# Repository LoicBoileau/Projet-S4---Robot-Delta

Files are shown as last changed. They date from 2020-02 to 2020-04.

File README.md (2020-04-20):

# Projet-S4---Robot-Delta
Projet de session hiver 2020 Équipe 1 Université de Sherbrooke - Robot Delta

## Licence MIT
Puisque notre projet est en open source, nous avons opté pour une licence MIT, car c'est une licence très permissive et très simple. Elle permet à tous les utilisateurs d'utiliser notre projet à leur guise, c'est-à-dire le modifier, le distribuer, l'utiliser à des fins commerciales ainsi que l'utiliser en privé. Toutefois, nous n'avons pas de garantie sur ce qui arrive avec ceux qui utilisent notre projet et ils ne peuvent pas nous poursuivre si jamais ils se blessent ou autre.

Pour une description complète de la License, voir le fichier License.

## Partie mécanique
Pour voir la liste des matériaux, les étapes d'assemblage du robot ainsi qu'une description des fichiers et des pièces, allez voir dans le fichier Robot_Delta_CAD.

## Partie vision
Pour voir le code de la vision, allez voir dans le fichier vision.

## Mathématiques du modèle
Une simulation physique a été conçue pour décrire la cinématique directe et inverse du robot.
-Disponible [ici](https://github.com/LoicBoileau/Projet-S4---Robot-Delta/tree/master/Simulations%20Physiques).

## Programmer les moteurs
Pour programmer les moteurs Dynamixel, il faut aller consulter le fichier "README" dans le répertoire "Controle_moteurs" 

## Requis pour l'Interface graphique
### Composantes
  - RaspberryPi avec python 3.4 installé (ou une version moins récente)
  - Python 3.4 32 bits installé sur un ordinateur pour programmer sur un ordinateur 
  - Librairies PySide et PySerial installées dans python 3.4 ou dans un environnement virtuel
  - IDE de programmation pour python (i.e. Visual Studio ou Visual Studio Code)
  
### Fonctionnement
L'interface graphique est codée en python et se compile à l'aide du fichier principal (GUI.py) et le fichier de widgets (mainwindow34.py et mainwindow34.ui
Le fichier mainwindow34.py est composé à partir du .ui qui lui se modifie à l'aide du designer.exe de QT. Donc pour modifier le fichier mainwindow34.py, 
il est nécessaire de suivre les instructions suivantes.

### Main pour Interface graphique
GUI.py est le main pour l'interface graphique et dépend du fichier de setup du UI appelé Mainwindow34.py

### Designer .UI
Pour accéder au designer de .ui de Qt, accéder au virtualEnvironnement ou le dossier contenant les librairies de python 3.4.
Dans le fichier, aller ensuite dans "Lib", "site-packages", "PySide"  et trouver le .exe appelé "designer.exe".

### Convertir .ui à .py 
Il est nécessaire de convertir le .ui à .py. Pour ce faire, aller dans le menu de VS "outils" ou "tools", ensuite aller dans "ligne de commande", 
"invite de commande développeur" et entrer les deux commandes suivantes :
* cd Controls
* pyside-uic Mainwindow.ui -o Mainwindow34.py

### Création de l'environnement virtuel à programmer
Pour programmer le UI, il faut un environnement virtuel qui contient les librairies utilisées. (PySide et PySerial)
Pour que les librairies soient disponibles, il est nécessaire de télécharger python3.4 32bits. Ensuite, soit par Visual Studio 
ou par l'invite de commande, installer les librairies.

### Installation des paquets sur le Raspberry Pi
* Installer l'image qui se trouve au lien suivant: https://github.com/UdeS-GRO/pi-gen et installer les paquets mentionnés dans le dossier stage5;
* Ensuite il faut installer python3.4 avec la commande: sudo apt-get install python3.4;
* Installer pip avec la commande: sudo apt-get install python3-pip;
* Installer PySide avec la commande: sudo apt-get install python3-pyside;
* Installer PySerial avec la commande: python3 -m pip install pyserial.

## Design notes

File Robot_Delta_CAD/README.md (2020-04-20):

# ReadMe pour les CAD du robot Delta.
## Descriptions des pièces de l'assemblage
* La plateforme supérieure sert à supporter l'ensemble du robot. 

* Les équerres permettent de soutenir les moteurs à la plateforme.

* Les moteurs utilisés sont les Dynamixel XL-430. 

* Le biceps est le premier bras (supérieur, celui qui est le plus court).

* L'avant-bras est le second bras (inférieur, celui qui est plus long) qui est d'une longueur de 25 cm.

* Les « *turnbuckles* » sont utilisés pour accorder plus de liberté au mouvement de rotation des biceps avec les avant-bras ainsi qu'aux avant-bras avec l'effecteur. Ils sont achetés tels quels au lien suivant: https://traxxas.com/products/parts/3745.

* Le « Fixateur_Bicep_Turnbuckle » sert à empêcher que le « *turnbuckle* » supérieur, celui attaché au biceps, puisse se déplacer horizontalement ou tourner. 

* Les gaines thermorétrécissables sont chauffées à l'aide d'un pistolet thermique « *Heat Gun* ». Son but est d'empêcher le mouvement vertical des avant-bras. 

* L'attache_Turnbuckle_Effecteur sert à relier le « *turnbuckle* » inférieur à l'effecteur.

* L'effecteur est la pince elle-même. 

* Le dossier « Piece_Electroaimant » contient toutes les pièces pour l'assemblage de l'électroaimant à l'effecteur. 

* Dechet_Poubelle et Dechet_Recyclage sont des déchets de différentes couleurs avec un aimant permettant au robot de les prendre avec l'électroaimant et de les trier dans les bacs correspondants. 

* Bac_Poubelle et Bac_Recyclage sont deux bacs permettant aux déchets d'être triés.

* Aluminium_Extrusion est la pièce qui a été utilisée pour faire l'assemblage de la base du robot. 

* Planche_De_Travail est la planche d'opération du robot, c'est-à-dire où les bacs ainsi que les déchets sont situés.

## Description des assemblages
* L'assemblage du robot est contenu dans le fichier « Assemblage_Robot_Delta ».

* L'assemblage pour l'environnement de travail du robot est dans le fichier « Assemblage_Robot_Delta_Avec_Base ».

## Méthodes de confection des pièces
* Toutes les pièces en bois sont découpées à l'aide d'une découpeuse laser. 

* Les autres pièces sont imprimées à l'aide d'une imprimante 3D.

## Étapes d'assemblage
1. Assembler la base du robot à l'aide des extrudés d'aluminium.

2. Ensuite, assembler les équerres à la plaque supérieure à l'aide de 2 vis M4 à tête cylindrique à six pans creux avec des écrous par équerre. Refaire cette opération trois fois.

3. Par la suite, assembler les moteurs aux équerres à l'aide de quatre vis M2 à tête cylindrique bombée à empreinte cruciforme et de rondelles « washer » par équerre. Refaire cette opération trois fois.

4. Assembler les biceps aux moteurs à l'aide de quatre vis M2 à tête cylindrique bombée à six pans creux, par moteur, qui filtre le bois du biceps lorsque la vis entre et qui se rend aux coupleurs du moteur. Refaire cette opération trois fois.

5. Assembler les « *turnbuckles* » aux biceps en enlevant un des bouts des « *turnbuckles* » pour qu'ils puissent s'insérer dans le trou du biceps. Refaire cette opération trois fois.

6. Remettre le bout enlevé des « *turnbuckles* ». Refaire cette opération trois fois.

7. Insérer le « Fixateur_Bicep_Turnbuckle » de chaque côté du biceps et le serrer à l'aide d'une vis M4 à tête cylindrique à six pans creux et d'un écrou par « Fixateur_Bicep_Turnbuckle », ce qui empêchera que les « *turnbuckles* » puissent se déplacer horizontalement ainsi que les rotations, sauf sur eux-mêmes. Refaire cette opération trois fois. 

8. Insérer « Attache_Turnbuckle_Effecteur » aux « *turnbuckles* » seulement en les poussant. Refaire cette opération trois fois. 

9. Insérer deux vis M4 à tête cylindrique à six pans creux avec des écrous par                       « Attache_Turnbuckle_Effecteur » pour empêcher le mouvement horizontal des « *turnbuckles* » ainsi que les mouvements de rotation, sauf sur eux-mêmes encore une fois. Refaire cette opération trois fois.

10. Insérer les six tiges (avant-bras) dans les trous des « *turnbuckles* ».

11. Découper les gaines thermorétrécissables en longueur de 1 cm 24 fois. (Quatre gaines thermorétrécissables par avant-bras).

12. Pour un avant-bras: chauffer les morceaux de gaines thermorétrécissables pour empêcher que les   « *turnbuckles* » sortent de la tige. Il faut donc chauffer un morceau de gaine thermorétrécissable à chaque bout de la tige et les deux autres morceaux sont espacés par les « *turnbuckles* ». Cela fait en sorte que les « *turnbuckles* » ne peuvent pas se déplacer en translation et qu'ils sont situés aux extrémités des avant-bras. 

13. Prendre l'électroaimant et l'insérer dans son support respectif. Si ce dernier tombe de son support, utiliser des vis M2 à tête cylindrique bombée à six pans creux pour qu'il reste en place.

14. Visser le support de l'électroaimant à l'effecteur à l'aide de quatre vis M4 à tête cylindrique à six pans creux avec des écrous.

15. Visser les « Attache_Turnbuckle_Effecteur » à l'effecteur à l'aide de deux vis M4 à tête cylindrique à six pans creux avec des écrous. Refaire cette opération trois fois. 

16. Attacher la plaque supérieure aux extrudés d'aluminium. 

## Liste des composantes *BOM (Bill Of Materials)*
1. 1 plaque supérieure en bois;
2. 3 équerres en plastique;
3. 3 moteurs dynamixel XL-430;
4. 3 biceps en bois;
5. 6 « Fixateur_Bicep_Turnbuckle » en plastique;
6. 6 « *turnbuckles* »;
7. 6 avant-bras de longueur de 25 cm en métal;
8. 3 « Attache_Turnbuckle_Effecteur » en plastique;
9. 1 électroaimant;
10. 24 morceaux de gaine thermorétrécissable de longueur de 1 cm;
11. 1 support à électroaimant en plastique;
12. 1 effecteur en bois;
13. 28 vis M4 à tête cylindrique à six pans creux avec des écrous respectifs;
14. 12 vis M2 à tête cylindrique bombée à six pans creux avec 12 rondelles respectives;
15. 12 vis M2 à tête cylindrique bombée à empreinte cruciforme.

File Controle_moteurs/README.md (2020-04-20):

### Programmer les moteurs
Pour programmer les moteurs Dynamixel, il faut le IDE d'Arduino avec la librairie de OpenCR.
Il faut également que les moteurs soient alimentés par une source d'alimentation externe, car l'alimentation fournie par le port USB de
l'ordinateur n'est pas suffisante au fonctionnement des moteurs.
La programmation n'est pas très complexe, puisque la librairie contient des exemples de codes qui 
permettent de facilement intégrer la fonctionnalité désirée. Les liens suivants dirigent vers les tutoriels appropriés.
Il est nécessaire de suivre les tutoriels afin d'identifier les moteurs. Afin de spécifier un déplacement des moteurs selon la 
position déterminée, il s'agit de copier dans le IDE d'Arduino le code Controle_Moteur qui permet d'utiliser les 3 moteurs contrairement 
à celui des librairies qui n'en contrôle qu'un seul.

http://emanual.robotis.com/docs/en/parts/controller/opencr10/
http://emanual.robotis.com/docs/en/software/dynamixel/dynamixel_workbench/

Les nombres spécifiés en paramètres dans la fonction "goalPosition" ne doivent pas dépasser 4096, qui est la résolution de chaque moteur.
Si une telle situation survient, il faut téléverser le programme à nouveau, car les moteurs vont tomber en "erreur". Pour un angle de
90 degrés, par exemple, il faut spécifier 1024 et ajuster par la suite, car la position 0 de chaque moteur n'est pas nécessairement la 
même. Il est également nécessaire de spécifier un délai minimal pour s'assurer que les moteurs atteignent leur position avant que le
prochain ne soit appelé.

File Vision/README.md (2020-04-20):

# ReadMe pour la vision.
## Étapes pour faire fonctionner la vision
* Installer pip avec la commande: sudo apt-get install python3-pip (si ce n'est pas fait);
* Installer la librairie OpenCV avec la commande: pip install opencv-python==3.4.1.15;
* Installer la librairie numpy avec la commande: pip install numpy;
* Installer la librairie csv avec la commande: pip install csv; 
* Se connecter au Raspberry Pi avec un écran et un clavier;
* Brancher la Webcam au RaspberryPi via la prise USB;
* Exécuter le code dans Python IDLE ou autre et prendre la planche de travail en photo lorsque souhaité;
* Pour la documentation du code allez voir les commentaires dans ce dernier.

## Informations utiles
* À cause de la distanciation sociale, il a été impossible d'intégrer la vision au robot c'est pourquoi la touche espace est présente pour prendre les photos. 

* Pour les tests, l'IDE PyCharm sur un ordinateur personnel a été utilisé, dans le but d'avoir plus de rapidité de traitement d'image ainsi qu'une meilleure qualité de caméra. Cependant, le code fonctionne très bien sur le Raspberry Pi. Il suffit d'utiliser Python IDLE et d'exécuter le code. 
  
## Sources utilisées
* Pour le calcul du centre de masse: https://www.learnopencv.com/find-center-of-blob-centroid-using-opencv-cpp-python/
* Pour l'algorithme de détection de contours: https://www.youtube.com/watch?v=6AY5p1uC5gM

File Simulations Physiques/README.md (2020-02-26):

# Simulations Physiques

DeltaRobot

## Simulation MotionGenesis

Logiciel de simulation physique, semblable à MatLab, permettant de faire des opérations vectorielles.
>Disponible [ici](http://www.motiongenesis.com/). 

 Est utilisé pour faire la cinématique directe et, éventuellement, la cinématique inverse.

### Cinématique directe
Description statique du robot. 
- Prend en **entrée** les angles &theta;<sub>1</sub>, &theta;<sub>2</sub> et &theta;<sub>3</sub> des moteurs.
- Donne en **sortie** la position P(x,y,z) de la "pince" du robot.

Est décrit par le fichier **MotionGenesis.txt**.

### Cinématique inverse
Description statique du robot. 
- Donne en **sortie** la position P(x,y,z) de la "pince" du robot.
- Prend en **entrée** les angles &theta;<sub>1</sub>, &theta;<sub>2</sub> et &theta;<sub>3</sub> des moteurs.

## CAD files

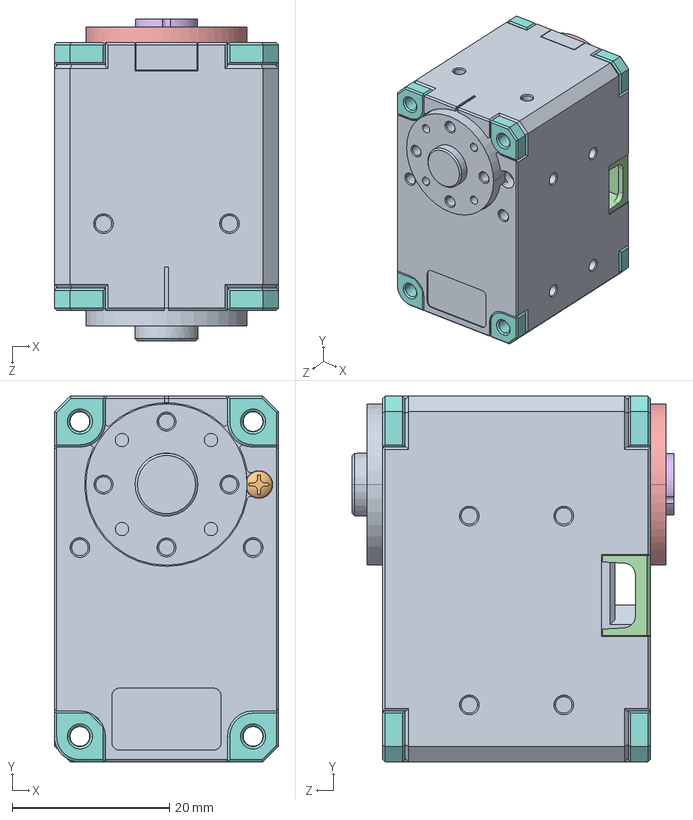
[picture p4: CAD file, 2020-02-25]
Robot_Delta_CAD/XL-430_new.SLDASM
28.5 x 46.5 x 40.9 mm
DC11_A01_DUMMY.stp
DX124_SCREW-COVER.stp
B3B-EH.stp x 2
DC11_A01_CASE_CVR_DUMMY.stp
DC11_A01_IDLER_DUMMY.stp
DC11_A01_IDLER_CAP_DUMMY.stp
DC11_A01_IDLER_SCREW.stp
DC11_A01_SPACER_DUMMY.stp x 8

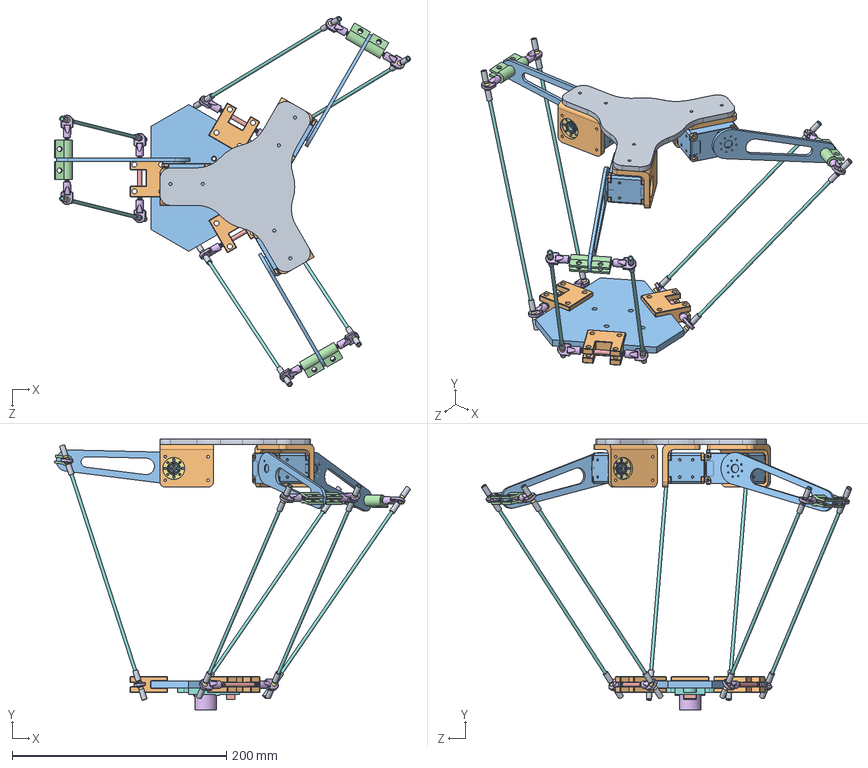
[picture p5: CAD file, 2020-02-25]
Robot_Delta_CAD/Assemblage_Robot_Delta.SLDASM
332.4 x 253.0 x 345.9 mm
Plaque_Support
Equerre_Moteur x 3
DC11_A01_DUMMY.stp x 3
DX124_SCREW-COVER.stp x 3
B3B-EH.stp x 6
DC11_A01_CASE_CVR_DUMMY.stp x 3
DC11_A01_IDLER_DUMMY.stp x 3
DC11_A01_IDLER_CAP_DUMMY.stp x 3
DC11_A01_IDLER_SCREW.stp x 3
DC11_A01_SPACER_DUMMY.stp x 24
Bicep x 3
Fixateur_Bicep_Turnbuckle x 6
Rod_Turnbuckle x 6
Attache_Rod_Boule_Turnbuckle x 12
Boule_Turnbuckle x 12
Avant_bras x 6
Gaine_Thermoretrecissable x 24
Attache_Turnbuckle_Effecteur x 3
Effecteur
PCB_Electroaimant
Connecteur_Electroaimant
Electroaimant
pan cross head screw_as
Support_Electroaimant

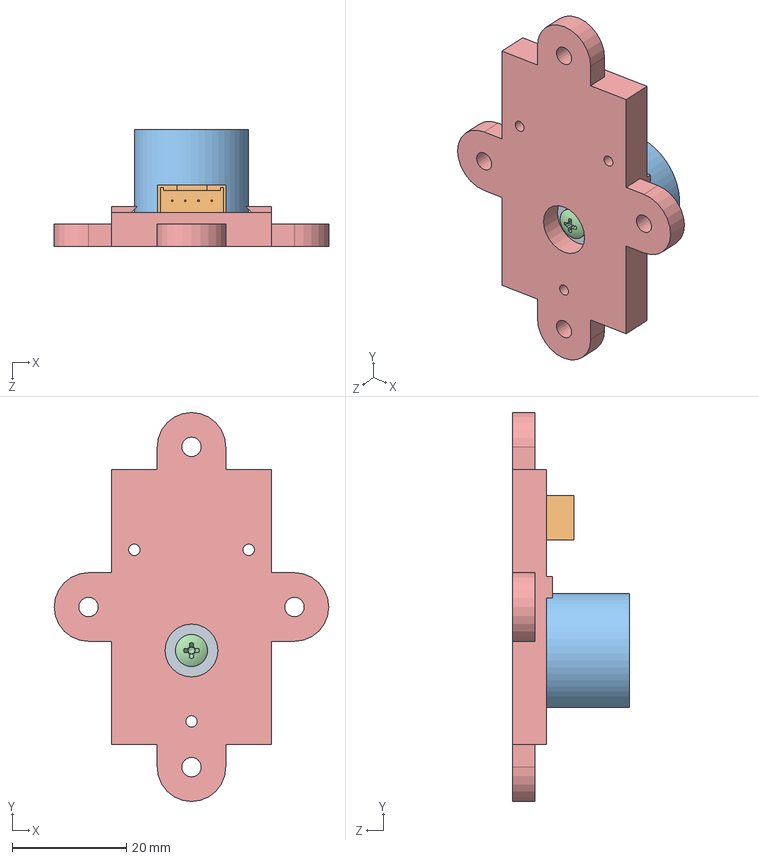
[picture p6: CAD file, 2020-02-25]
Robot_Delta_CAD/Piece_Electroaimant/Assemblage_Electroaimant.SLDASM
48.0 x 68.0 x 20.5 mm
PCB_Electroaimant
Connecteur_Electroaimant
Electroaimant
pan cross head screw_as
Support_Electroaimant

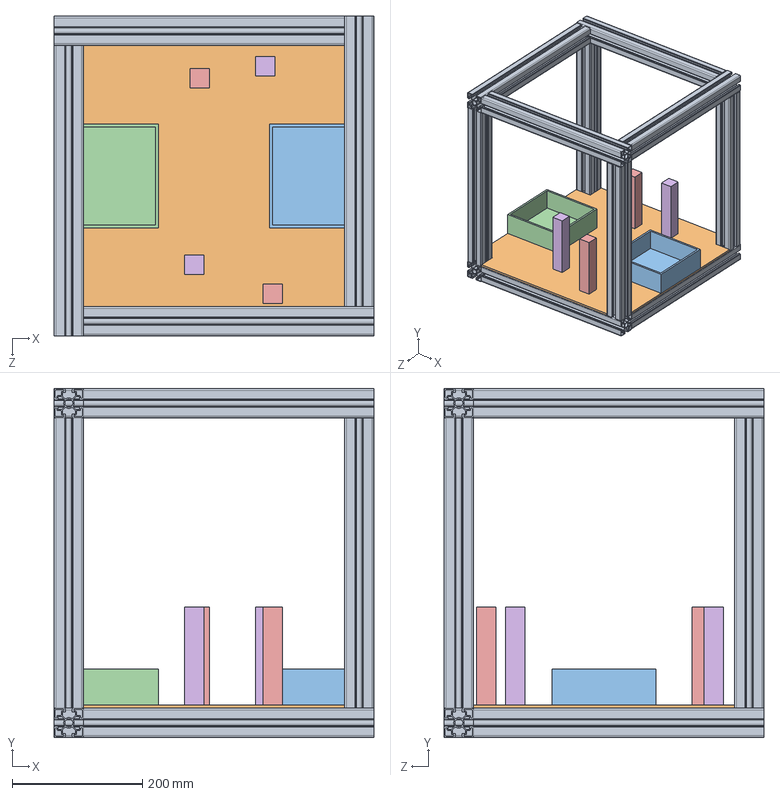
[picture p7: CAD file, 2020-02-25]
Robot_Delta_CAD/Assemblage_Robot_Delta_Avec_Base.SLDASM
490.0 x 535.0 x 490.0 mm
Aluminium_Extrusion x 12
Planche_De_Travail
Bac_Poubelle
Bac_Recyclage
Dechet_Poubelle x 2
Dechet_Recyclage x 2

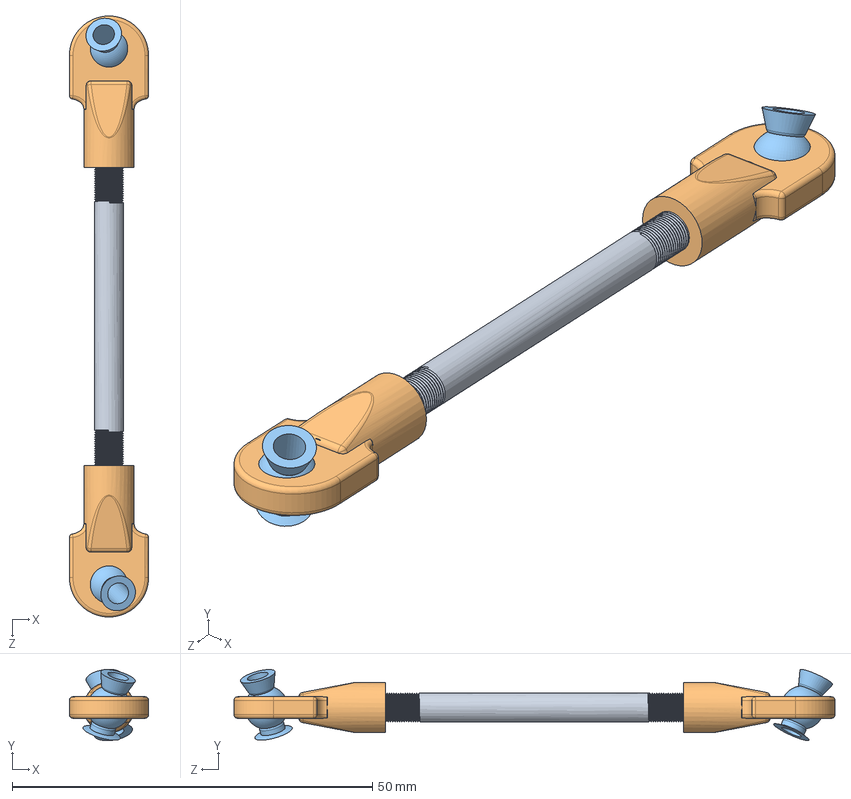
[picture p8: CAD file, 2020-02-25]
Robot_Delta_CAD/Turnbuckle.SLDASM
11.0 x 9.90 x 83.4 mm
Rod_Turnbuckle
Attache_Rod_Boule_Turnbuckle x 2
Boule_Turnbuckle x 2

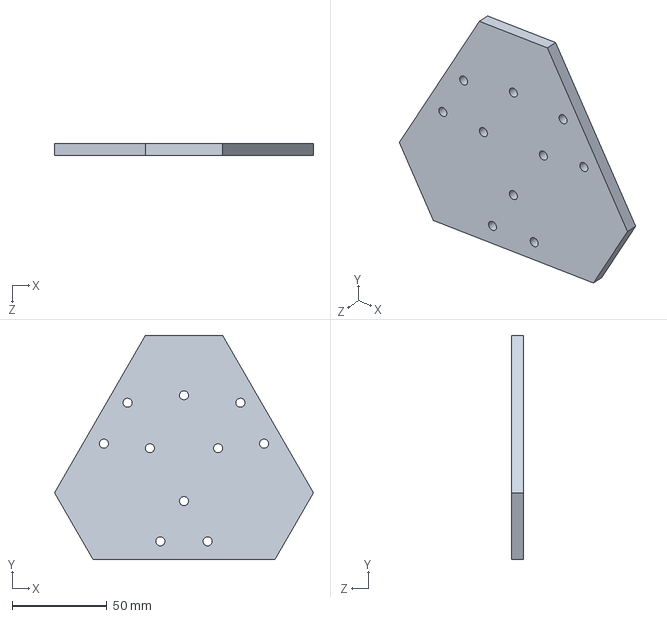
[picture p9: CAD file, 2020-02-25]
Robot_Delta_CAD/Effecteur.SLDPRT
137.0 x 118.6 x 6.35 mm

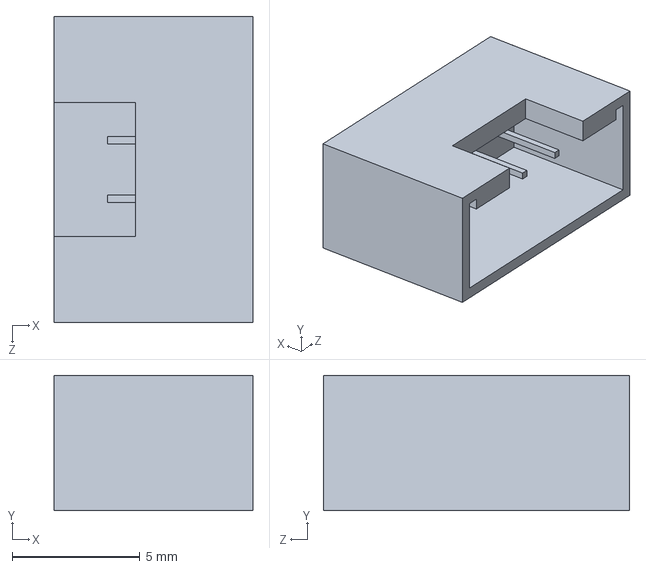
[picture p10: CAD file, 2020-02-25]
Robot_Delta_CAD/Piece_Electroaimant/Connecteur_Electroaimant.SLDPRT
7.80 x 5.30 x 12.0 mm

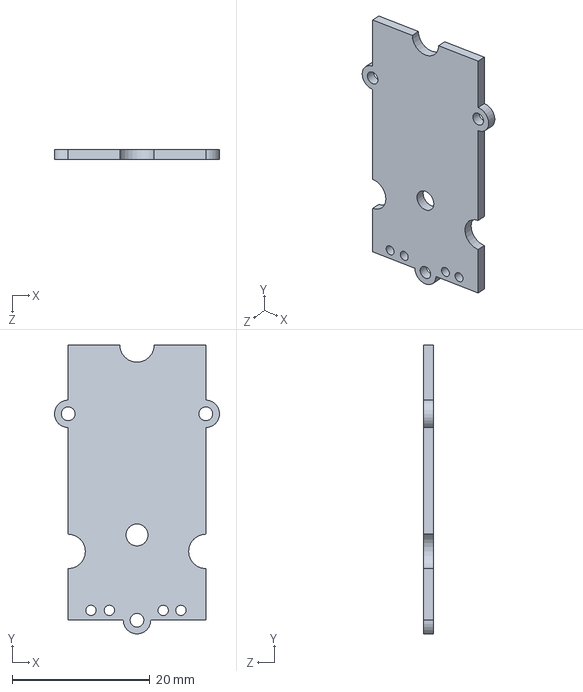
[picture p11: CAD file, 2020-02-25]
Robot_Delta_CAD/Piece_Electroaimant/PCB_Electroaimant.SLDPRT
24.0 x 42.0 x 1.50 mm

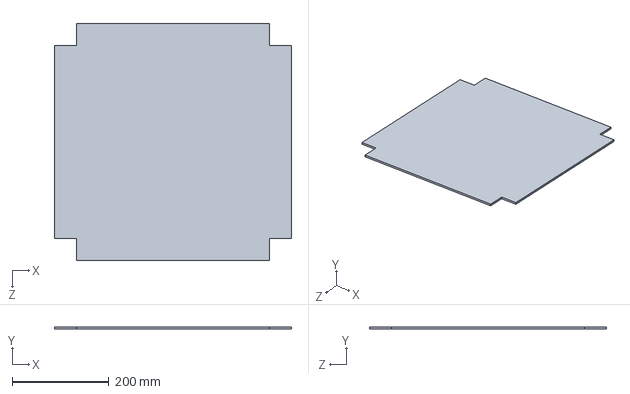
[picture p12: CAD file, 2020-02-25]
Robot_Delta_CAD/Planche_De_Travail.SLDPRT
490.0 x 5.00 x 490.0 mm

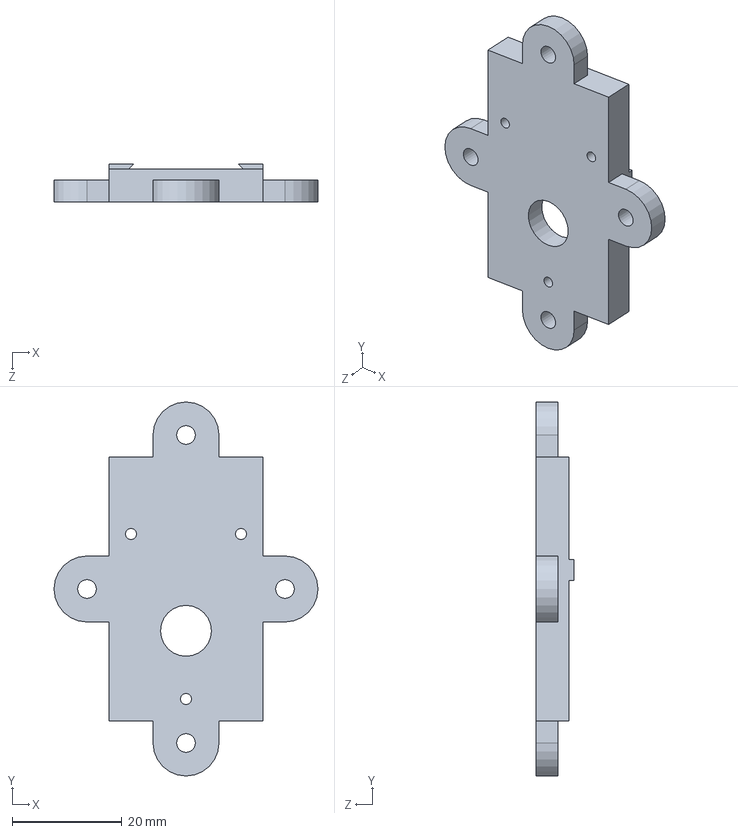
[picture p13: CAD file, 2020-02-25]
Robot_Delta_CAD/Piece_Electroaimant/Support_Electroaimant.sldprt
48.0 x 68.0 x 7.00 mm

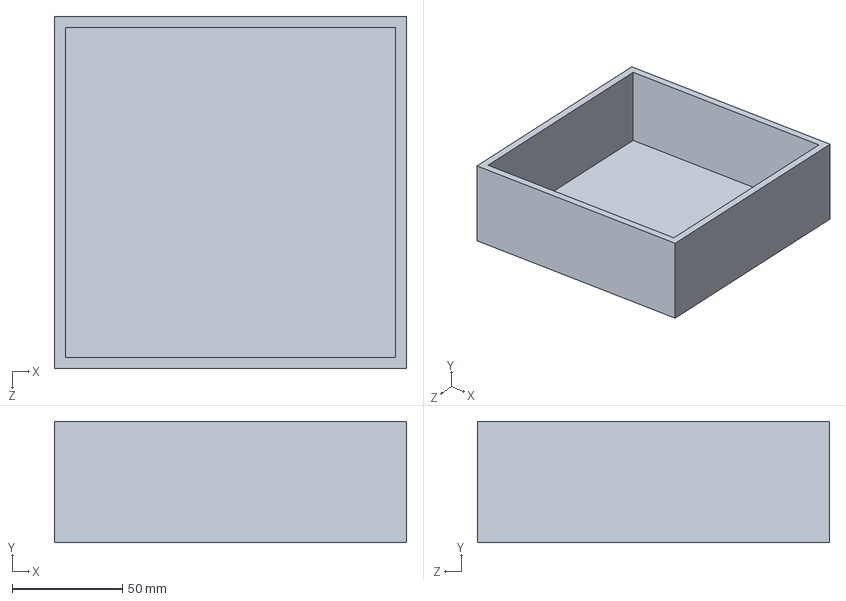
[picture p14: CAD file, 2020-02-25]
Robot_Delta_CAD/Bac_Recyclage.SLDPRT
160.0 x 55.0 x 160.0 mm

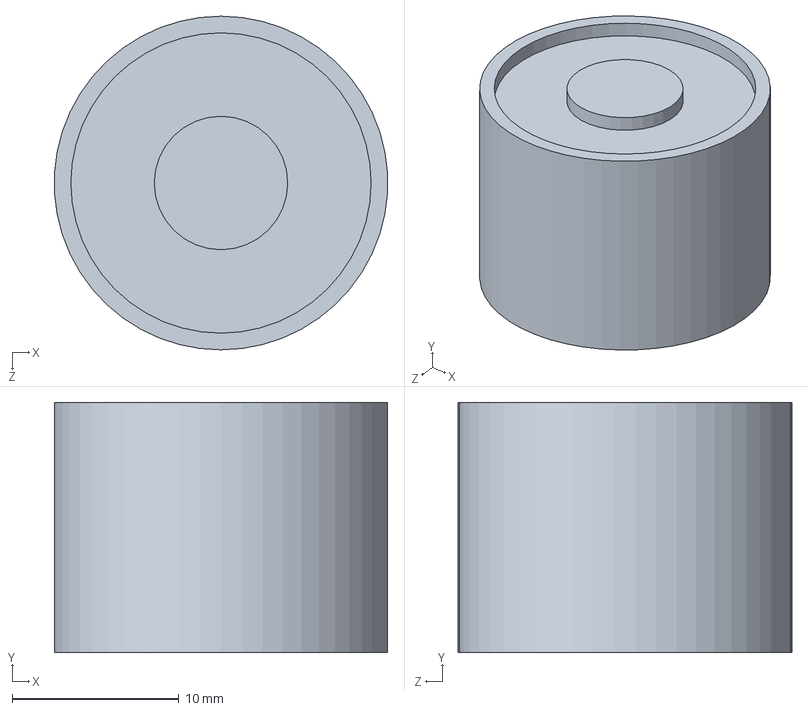
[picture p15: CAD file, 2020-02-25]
Robot_Delta_CAD/Piece_Electroaimant/Electroaimant.SLDPRT
20.0 x 15.0 x 20.0 mm

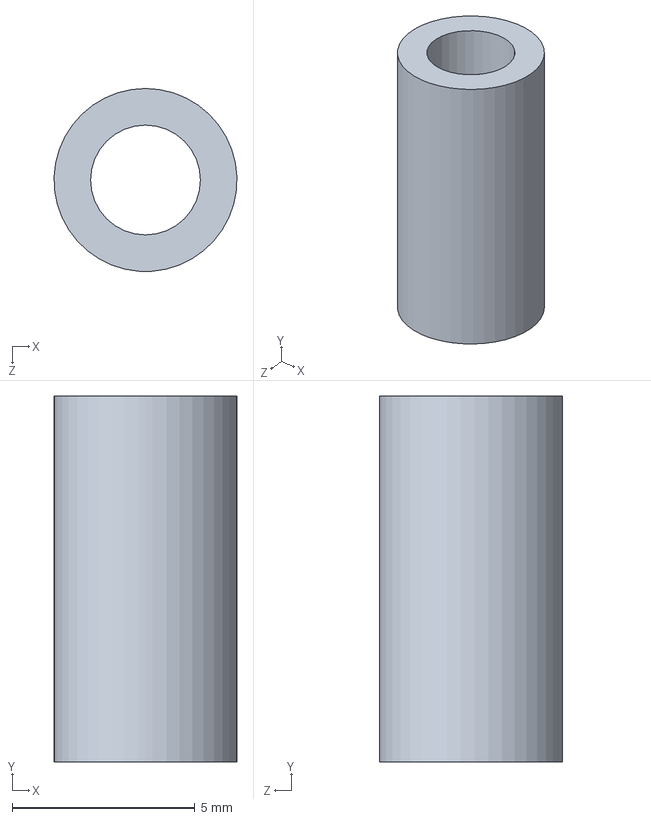
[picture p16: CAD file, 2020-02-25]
Robot_Delta_CAD/Gaine_Thermoretrecissable.SLDPRT
5.00 x 10.0 x 5.00 mm

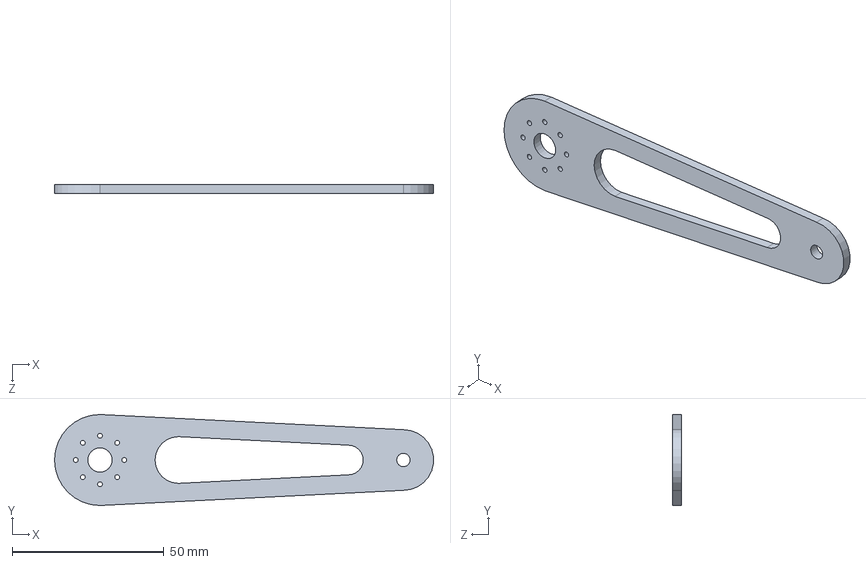
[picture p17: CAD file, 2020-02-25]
Robot_Delta_CAD/Bicep.SLDPRT
124.9 x 30.0 x 3.00 mm

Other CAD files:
Robot_Delta_CAD/Avant_bras.SLDPRT
Robot_Delta_CAD/Dechet_Recyclage.SLDPRT
Robot_Delta_CAD/Plaque_Support.SLDPRT
Robot_Delta_CAD/Bac_Poubelle.SLDPRT
Robot_Delta_CAD/Aluminium_Extrusion.SLDPRT
Robot_Delta_CAD/Attache_Rod_Boule_Turnbuckle.SLDPRT
Robot_Delta_CAD/Attache_Turnbuckle_Effecteur.SLDPRT
Robot_Delta_CAD/Boule_Turnbuckle.SLDPRT
Robot_Delta_CAD/Dechet_Poubelle.SLDPRT
Robot_Delta_CAD/Equerre_Moteur.SLDPRT
Robot_Delta_CAD/Fixateur_Bicep_Turnbuckle.SLDPRT
Robot_Delta_CAD/Rod_Turnbuckle.SLDPRT

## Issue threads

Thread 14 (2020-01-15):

Faire tourner les moteurs

nguwuyen, 2020-01-15:

alexfilion, 2020-02-19:
Trouver sur Visual Studio comment envoyer un certain courant au moteur pour le faire tourner.
Faire des tests pour comprendre son encodeur et pouvoir l'arrêter à la valeur que l'on veut.

Closed 2020-02-21.

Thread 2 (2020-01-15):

En tant qu'utilisateur, je veux que le robot soit supporté à un point fixe

LoicBoileau, 2020-01-15:
- Structure en Aluminium (idée)

nguwuyen, 2020-02-13:
Frame

Closed 2020-04-17.

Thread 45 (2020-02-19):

Cinématique Direct

alexfilion, 2020-02-19:
Faire les mathématiques pour trouver les coordonnées du robot selon des angles que les moteurs ont.
Trouver les équations les reliant.

alexfilion, 2020-02-19:
Faire les mathématiques pour trouver les angles des moteurs si on donne une coordonnée.
Trouver les équations les reliant.

Closed 2020-04-01.

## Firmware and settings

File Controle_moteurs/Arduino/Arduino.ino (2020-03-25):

/* Authors: Loic Boileau */

#include <DynamixelWorkbench.h>

#if defined(__OPENCM904__)
  #define DEVICE_NAME "3" //Dynamixel on Serial3(USART3)  <-OpenCM 485EXP
#elif defined(__OPENCR__)
  #define DEVICE_NAME ""
#endif   

#define BAUDRATE        57600
#define DXL_ID1         2
#define DXL_ID2         3
#define DXL_ID3         1

#define LENGTH_MESSAGE  8
#define DECA_MOT3       200

uint8_t dxl_id1 = DXL_ID1;
uint8_t dxl_id2 = DXL_ID2;
uint8_t dxl_id3 = DXL_ID3;

int32_t theta1 = 0;
int32_t theta2 = 0;
int32_t theta3 = 0;

int32_t msgArg1 = 0;
int32_t msgArg2 = 0;
int32_t msgArg3 = 0;

int cmdNb = 0;

uint32_t maxPosMotor1 = 2500;
uint32_t maxPosMotor2 = 2500;
uint32_t maxPosMotor3 = 2500;

uint32_t minPosMotor1 = 1000;
uint32_t minPosMotor2 = 1000;
uint32_t minPosMotor3 = 800; //valeur des autres moteurs - DECA_MOT3(200)

DynamixelWorkbench dxl_wb;

bool commandReceived = false;

void setup() 
{  
  Serial.begin(57600);
  // while(!Serial); // Wait for Opening Serial Monitor

  Serial.println('Reset of the Open CR');

  const char *log;
  bool result = false;
  
  uint16_t model_number_id1 = 0;
  uint16_t model_number_id2 = 0;
  uint16_t model_number_id3 = 0;

  float decalage_id1 = 0;

  result = dxl_wb.init(DEVICE_NAME, BAUDRATE, &log);
  if (result == false)
  {
    Serial.println(log);
    Serial.println("Failed to init");
  }
  else
  {
    Serial.print("Succeeded to init : ");
    Serial.println(BAUDRATE);  
  }

  result = dxl_wb.ping(dxl_id1, &model_number_id1, &log)&& dxl_wb.ping(dxl_id2, &model_number_id2, &log) && dxl_wb.ping(dxl_id3, &model_number_id3, &log) ;
  if (result == false)
  {
    Serial.println(log);
    Serial.println("Failed to ping");
  }
  else
  {
    Serial.println("Succeeded to ping");
    Serial.print("id motor1 : ");
    Serial.print(dxl_id1);
    Serial.print(" model_number : ");
    Serial.println(model_number_id1);
    Serial.print("id motor2 : ");
    Serial.print(dxl_id2);
    Serial.print(" model_number : ");
    Serial.println(model_number_id2);
    Serial.print("id motor3 : ");
    Serial.print(dxl_id3);
    Serial.print(" model_number : ");
    Serial.println(model_number_id3);
  }

  result = dxl_wb.jointMode(dxl_id1, 0, 0, &log) && dxl_wb.jointMode(dxl_id2, 0, 0, &log) && dxl_wb.jointMode(dxl_id3, 0, 0, &log);
  if (result == false)
  {
    Serial.println(log);
    Serial.println("Failed to change joint mode");
  }
  else
  {
    Serial.println("Succeed to change joint mode");
    Serial.println("Dynamixel is moving...");

    for (int count = 0; count < 1; count++)
    {
      dxl_wb.goalPosition(dxl_id1, (int32_t)1000);
      dxl_wb.goalPosition(dxl_id2, (int32_t)1000);
      dxl_wb.goalPosition(dxl_id3, (int32_t)800);
      delay(3000);

      dxl_wb.goalPosition(dxl_id1, (int32_t)2000);
      dxl_wb.goalPosition(dxl_id2, (int32_t)2000);
      dxl_wb.goalPosition(dxl_id3, (int32_t)1800);
      delay(3000);
    }
  }
  
}

void loop() 
{

  if (Serial.available() > 0){
    cmdNb = readData(); //read the available data and return the first short received as the command number

    if ( cmdNb >= 1 ) //make sure the angle received are in a good range and command is for moving motors
      Serial.write((byte)cmdNb);  //write the command Number to confirmed you have received it
      theta1 = msgArg1;
      theta2 = msgArg2;
      theta3 = msgArg3;
      commandReceived = true;
      delay(10);
    }
    else if( cmdNb == 1 ){ //if the command is for something else then dont activate the motors
      Serial.write((byte)cmdNb);
      delay(10);
    }
  
  if (commandReceived){
    checkMaxPosMotors();
        
    dxl_wb.goalPosition(dxl_id1, (int32_t)theta1);
    dxl_wb.goalPosition(dxl_id2, (int32_t)theta2);
    dxl_wb.goalPosition(dxl_id3, (int32_t)theta3-DECA_MOT3);
    
    commandReceived = false;
  }
}

int readData()
{
  byte bytesBuffer[LENGTH_MESSAGE];
  int i = 0;
  while (Serial.available()) {
    delay(10);  
    if (Serial.available() >0) {
      byte Byte = Serial.read();  //gets one byte from serial buffer
      bytesBuffer[i++] = Byte; //makes the string readString
      //Serial.println(bytesBuffer[i]);
    }  
  }
  //Prendre le premier octet et le décaller de 8 bits.
  int commandNb = int((unsigned char)(bytesBuffer[1]) << 8 | (unsigned char)(bytesBuffer[0]));
  
  msgArg1 = int((unsigned char)(bytesBuffer[3]) << 8 | (unsigned char)(bytesBuffer[2])); 
  msgArg2 = int((unsigned char)(bytesBuffer[5]) << 8 | (unsigned char)(bytesBuffer[4]));
  msgArg3 = int((unsigned char)(bytesBuffer[7]) << 8 | (unsigned char)(bytesBuffer[6]));

  return (commandNb);
}

bool checkMaxPosMotors()
{
  bool motorCommandInRange = true;
  if (theta1 > maxPosMotor1){
    theta1 = maxPosMotor1;
    motorCommandInRange = false;
  }
  else if (theta1 < minPosMotor1){
    theta1 = minPosMotor1;
    motorCommandInRange = false;
  }
  if (theta2 > maxPosMotor2){
    theta2 = maxPosMotor2;
    motorCommandInRange = false;
  }
  else if (theta2 < minPosMotor2){
    theta2 = minPosMotor2;
    motorCommandInRange = false;
  }
  if (theta3 > maxPosMotor3){
    theta3 = maxPosMotor3;
    motorCommandInRange = false;
  }
  else if (theta3 < minPosMotor3){
    theta3 = minPosMotor3;
    motorCommandInRange = false;
  }
  return (motorCommandInRange);
}

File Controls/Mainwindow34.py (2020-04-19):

# -*- coding: utf-8 -*-

# Form implementation generated from reading ui file 'Mainwindow.ui'
#
# Created: Sat Apr 18 12:41:44 2020
#      by: pyside-uic 0.2.15 running on PySide 1.2.4
#
# WARNING! All changes made in this file will be lost!

from PySide import QtCore, QtGui

class Ui_MainWindow(object):
    def setupUi(self, MainWindow):
        MainWindow.setObjectName("MainWindow")
        MainWindow.setEnabled(True)
        MainWindow.resize(849, 724)
        self.centralwidget = QtGui.QWidget(MainWindow)
        self.centralwidget.setObjectName("centralwidget")
        self.line = QtGui.QFrame(self.centralwidget)
        self.line.setGeometry(QtCore.QRect(341, 201, 0, 0))
        self.line.setFrameShape(QtGui.QFrame.HLine)
        self.line.setFrameShadow(QtGui.QFrame.Sunken)
        self.line.setObjectName("line")
        self.label_5 = QtGui.QLabel(self.centralwidget)
        self.label_5.setGeometry(QtCore.QRect(40, 14, 80, 20))
        self.label_5.setObjectName("label_5")
        self.comboBoxPort = QtGui.QComboBox(self.centralwidget)
        self.comboBoxPort.setGeometry(QtCore.QRect(90, 15, 221, 20))
        self.comboBoxPort.setObjectName("comboBoxPort")
        self.frame_command1 = QtGui.QFrame(self.centralwidget)
        self.frame_command1.setGeometry(QtCore.QRect(30, 40, 431, 581))
        self.frame_command1.setStyleSheet("")
        self.frame_command1.setFrameShape(QtGui.QFrame.StyledPanel)
        self.frame_command1.setFrameShadow(QtGui.QFrame.Raised)
        self.frame_command1.setObjectName("frame_command1")
        self.label_theta1 = QtGui.QLabel(self.frame_command1)
        self.label_theta1.setGeometry(QtCore.QRect(190, 164, 56, 20))
        self.label_theta1.setAlignment(QtCore.Qt.AlignCenter)
        self.label_theta1.setObjectName("label_theta1")
        self.lineEdit_x = QtGui.QLineEdit(self.frame_command1)
        self.lineEdit_x.setGeometry(QtCore.QRect(45, 54, 130, 20))
        self.lineEdit_x.setStyleSheet("background-color: rgb(255, 255, 255);")
        self.lineEdit_x.setObjectName("lineEdit_x")
        self.button_command = QtGui.QPushButton(self.frame_command1)
        self.button_command.setGeometry(QtCore.QRect(12, 510, 235, 61))
        font = QtGui.QFont()
        font.setPointSize(11)
        self.button_command.setFont(font)
        self.button_command.setStyleSheet("#button_command{\n"
"border: 2px solid;\n"
"background-color: white;\n"
"    border-top-color: rgb(85, 255, 0);\n"
"    border-left-color: rgb(85, 255, 0);\n"
"    border-right-color: rgb(67, 203, 0);\n"
"    border-bottom-color: rgb(67, 203, 0);\n"
"}\n"
"#button_command:pressed{\n"
"    background-color: rgb(85, 255, 0);\n"
"}")
        self.button_command.setObjectName("button_command")
        self.lineEdit_ChangeCommand = QtGui.QLineEdit(self.frame_command1)
        self.lineEdit_ChangeCommand.setGeometry(QtCore.QRect(310, 370, 51, 41))
        font = QtGui.QFont()
        font.setPointSize(11)
        self.lineEdit_ChangeCommand.setFont(font)
        self.lineEdit_ChangeCommand.setStyleSheet("background-color: rgb(255, 255, 255);")
        self.lineEdit_ChangeCommand.setAlignment(QtCore.Qt.AlignCenter)
        self.lineEdit_ChangeCommand.setObjectName("lineEdit_ChangeCommand")
        self.checkBox_cinDir = QtGui.QCheckBox(self.frame_command1)
        self.checkBox_cinDir.setGeometry(QtCore.QRect(12, 26, 411, 20))
        font = QtGui.QFont()
        font.setPointSize(9)
        self.checkBox_cinDir.setFont(font)
        self.checkBox_cinDir.setObjectName("checkBox_cinDir")
        self.lineEdit_y = QtGui.QLineEdit(self.frame_command1)
        self.lineEdit_y.setGeometry(QtCore.QRect(45, 80, 130, 20))
        self.lineEdit_y.setStyleSheet("background-color: rgb(255, 255, 255);")
        self.lineEdit_y.setObjectName("lineEdit_y")
        self.label_z = QtGui.QLabel(self.frame_command1)
        self.label_z.setGeometry(QtCore.QRect(190, 106, 56, 20))
        self.label_z.setAlignment(QtCore.Qt.AlignCenter)
        self.label_z.setObjectName("label_z")
        self.label_6 = QtGui.QLabel(self.frame_command1)
        self.label_6.setGeometry(QtCore.QRect(10, 5, 411, 20))
        font = QtGui.QFont()
        font.setPointSize(9)
        self.label_6.setFont(font)
        self.label_6.setAlignment(QtCore.Qt.AlignCenter)
        self.label_6.setObjectName("label_6")
        self.label_x = QtGui.QLabel(self.frame_command1)
        self.label_x.setGeometry(QtCore.QRect(190, 54, 56, 20))
        self.label_x.setAlignment(QtCore.Qt.AlignCenter)
        self.label_x.setObjectName("label_x")
        self.checkBox_cinInv = QtGui.QCheckBox(self.frame_command1)
        self.checkBox_cinInv.setGeometry(QtCore.QRect(12, 136, 411, 20))
        font = QtGui.QFont()
        font.setPointSize(9)
        self.checkBox_cinInv.setFont(font)
        self.checkBox_cinInv.setObjectName("checkBox_cinInv")
        self.EStop = QtGui.QPushButton(self.frame_command1)
        self.EStop.setGeometry(QtCore.QRect(12, 296, 411, 60))
        font = QtGui.QFont()
        font.setPointSize(22)
        self.EStop.setFont(font)
        self.EStop.setStyleSheet("#EStop {\n"
"border: 2px solid;\n"
"border-radius: 6px;\n"
"\n"
"color: red;\n"
"    border-top-color: rgb(255, 0, 0);\n"
"    border-right-color: rgb(202, 0, 0);\n"
"    border-bottom-color: rgb(202, 0, 0);\n"
"    border-left-color: rgb(255, 0, 0);\n"
"background-color: pink;\n"
"}\n"
"#EStop:pressed \n"
"{ \n"
"background-color: white;\n"
"}")
        self.EStop.setObjectName("EStop")
        self.label_theta3 = QtGui.QLabel(self.frame_command1)
        self.label_theta3.setGeometry(QtCore.QRect(190, 216, 56, 20))
        self.label_theta3.setAlignment(QtCore.Qt.AlignCenter)
        self.label_theta3.setObjectName("label_theta3")
        self.lineEdit_z = QtGui.QLineEdit(self.frame_command1)
        self.lineEdit_z.setGeometry(QtCore.QRect(45, 106, 130, 20))
        self.lineEdit_z.setStyleSheet("background-color: rgb(255, 255, 255);")
        self.lineEdit_z.setObjectName("lineEdit_z")
        self.label_y = QtGui.QLabel(self.frame_command1)
        self.label_y.setGeometry(QtCore.QRect(190, 80, 56, 20))
        self.label_y.setAlignment(QtCore.Qt.AlignCenter)
        self.label_y.setObjectName("label_y")
        self.pushButton_Params = QtGui.QPushButton(self.frame_command1)
        self.pushButton_Params.setGeometry(QtCore.QRect(12, 256, 411, 26))
        self.pushButton_Params.setObjectName("pushButton_Params")
        self.label_theta2 = QtGui.QLabel(self.frame_command1)
        self.label_theta2.setGeometry(QtCore.QRect(190, 190, 56, 20))
        self.label_theta2.setAlignment(QtCore.Qt.AlignCenter)
        self.label_theta2.setObjectName("label_theta2")
        self.button_command_Stop = QtGui.QPushButton(self.frame_command1)
        self.button_command_Stop.setGeometry(QtCore.QRect(323, 510, 100, 61))
        font = QtGui.QFont()
        font.setPointSize(14)
        self.button_command_Stop.setFont(font)
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

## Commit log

2020-01-15 Ajout d'un dossier CAD
2020-01-15 Ajouter fichier texte dans CAD
2020-01-15 Clarifier dossier CAD
2020-02-05 Ajout d'un nouveau fichier python pour le GUI de Qt
2020-02-05 Ajout du fichier GUI.UI dans la solution
2020-02-11 Ajout d'un environnement virtuel en python 3 au cas ou. Ajout du logiciel UI designer de Qt, voir readMe pour trouver la location du fichier.
    [pyvenv.cfg]
2020-02-13 Modification du UI avec Phil, ajout arrêt d'urgence et boutton de commande
2020-02-15 Modification de la location du fichier designer.exe et ajout d'un code pour executer l'interface graphique
2020-02-15 Ajout du fichier .exe pour convertir les fichir .ui en .py. Il suffit simplement d'utiliser la commande dans le fichier readMe
2020-02-16 Ajout d'un main pour l'interface graphiqe. Ajout de la commande pour convertir .ui à .py dans le readMe.
2020-02-16 Régler issue #26 faire clignoter le EStop
    [GUI.py]
2020-02-17 Ajout d'un boutton pour confirmer les coordonnées cartésiennes
2020-02-18 Ajout d'un gestionnaire de thread et d'une loop de temps qui vérifiera à chaque 0.1 s si l'interface graphique c'est fait updater. Modification du fichier requirement.txt
2020-02-18 ajout de checkbox exclusive pour cinematique directe et inverse
2020-02-18 Ajout d'une option de synchronisation pour les ports
2020-02-19 Retirer environnement virtuel RaspberryPi
    [pyvenv.cfg]
2020-02-21 Ajout de fonctionnalitées pour le UI dont le boutton pour envoyer une commande
2020-02-23 Create README.txt pour les CAD du robot
2020-02-23 Ajout de tous les CAD du robot
    [Aluminium_Extrusion.SLDPRT, Assemblage_Electroaimant.SLDASM, Assemblage_Robot_Delta.SLDASM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]
2020-02-23 Création d'un README pour les CAD
2020-02-23 Correction de turbuckle pour turnbuckle
2020-02-23 Ajout du MotionGenesis
    Simulation partielle. Celle-ci permet de décrire la dynamique des bras du robot pour un déplacement sur la hauteur ( axe Ny> ). Pas encore en mesure de déduire le déplacement de la pince en fonction 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
2020-02-24 Mise à jour du README pour l'assemblage du robot
2020-02-25 Ajout de la librairie struct
2020-02-25 Create Controle_Moteur
    Code en C pour contrôler les trois moteurs du robot
2020-02-25 Ajout des requis pour interface graphique
2020-02-25 BOM et etapes d'assemblage dans le README
2020-03-10 Add the libraries to the folder for the motors
    [controltable.ods]
2020-03-10 add the main file for the motor controls
2020-03-10 ajouter arduino.ino
2020-03-10 supprimer fichiers mauvaise librairie
    [controltable.ods]
2020-03-12 Ajout d'une option pour la communication entre PI et Open CR
2020-03-16 Ajout du module de communication et modifications du code
2020-03-17 Modification sur le code d'Arduino
2020-03-18 Modification sur le code Arduino et le code python
2020-04-01 Update CinematiqueInverse.m
    Ajout d'une correction sur les positions
2020-04-05 Ajout d'une fonction de calcul d'angle selon les coordonnées cartésiennes, ajout d'un thread d'envoi de cordonnées cartésiennes, ajout d'une fonction d'envoi de coordonnées cartésiennes, ajout de com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
2020-04-08 Script de la caméra
2020-04-20 Ajout de commentaire dans le code
2020-04-20 Retirer les fichiers parasites
